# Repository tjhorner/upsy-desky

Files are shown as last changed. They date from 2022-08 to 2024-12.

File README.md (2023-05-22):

# Upsy Desky 

This repository contains the source files for the Upsy Desky, a device which lets you connect your standing desk to any home automation system.

You can buy one on Tindie:



## Need Support?

If you need help with your Upsy Desky, please join the Upsy Desky [Discord server](https://discord.gg/ZHfXKQrSxF) where you can ask for help from the community and myself.

## Repository Structure

At the root of the repository you will find these directories:

- `pcb`: KiCad schematic and PCB design files (CC BY-NC-SA 4.0)
- `enclosure`: Fusion 360 design files and STLs for the enclosure (CC BY-NC-SA 4.0)
- `firmware`: ESPHome configuration files for the stock firmware (MIT)

With these you can make your own Upsy Desky from scratch, or you can make changes to the design and firmware to suit your needs. (If you do, I would love to see it!)

## What's new‽

This is the successor to the [WiFi Standing Desk Controller](https://github.com/tjhorner/wifi-desk-controller), packed with improvements and bug fixes — most notably:

- USB-C port for easy flashing (and because USB-C is cool 😎)
- Runtime firmware configuration -- no more manual flashing or compiling ESPHome to change stuff
- Improved enclosure design with a more snug fit and screw-mounted PCB, allowing for easier repairs and troubleshooting
- Replacing the D1 Mini with an ESP32-WROOM module, providing hardware UART for more reliable desk connection
- A catchier name, because "WiFi Standing Desk Controller" was a mouthful

This revision also fixes some annoying issues from the first version, such as the desk sometimes lowering on startup, or simply not powering at all without a hacky workaround.

## In a nutshell...

As with the original version of this product, it can connect your motorized standing desk to your home automation system. It can read your desk's current height, and set it as well. This lets you create automations that integrate with your desk, for example:

- If you're sitting for too long, raise desk to standing height
- When you leave home, raise desk to max height so the cat can't knock things over
- Have an infinite number of presets for everyone in your household
- Send desk height data to InfluxDB to analyze how often you're sitting vs. standing
- [Publish your desk's height on the internet](https://tjhorner.dev/sitting-or-standing/)

Or whatever else you'd like. The possibilities are endless! As long as the possibilities involve a standing desk.

## Compatibility

Any standing desk that uses RJ45 to connect to the keypad is likely compatible, but the control boxes listed [here](https://upsy-desky.tjhorner.dev/docs/reference/compatibility/) are verified to be compatible.

## Documentation

You can find everything you need in the [documentation](https://upsy-desky.tjhorner.dev/docs/getting-started/).

## Licenses

The ESPHome configs are licensed under MIT; everything else (enclosure and PCB design) are CC BY-NC-SA 4.0. The appropriate license files are available in the root of the repo.

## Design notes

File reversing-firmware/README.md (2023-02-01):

# Reverse Engineering Firmware

This is a special firmware designed to aid in the reverse engineering of new desk control box protocols. You can find the complete reverse engineering guide [here](https://upsy-desky.tjhorner.dev/docs/advanced/reverse-engineering/).

You can flash this firmware on your stock Upsy Desky; no additional hardware is required. It uses ESPHome's [UART debugging feature](https://esphome.io/components/uart.html#debugging) to log all communication between the keypad and control box. You can use this data to reverse engineer the protocol based on the RE guide linked above.

## Customization

Aside from the normal UART parameters like baud rate, it may be helpful to adjust the parameters in the UART debugging component to make the data more readable and easier to RE. Particularly useful is the `after` parameter, which allows you to log a string of bytes after some specified number of bytes, timeout, or delimiter. You can see the specific configuration options in the [ESPHome documentation](https://esphome.io/components/uart.html#debugging).

You may also wish to change the GPIO port to match the RX and TX pins on your control box if the defaults don't match yours. See the [GPIO Pinout](https://upsy-desky.tjhorner.dev/docs/reference/gpio/) mapping to see which RJ45 pins correspond to which GPIO pins.

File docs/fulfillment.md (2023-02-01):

# Order Fulfillment Process

I wrote this out in order to help my future self if I ever go on hiatus or something. But it could be useful if you're starting to sell a similar product and are wondering what the process is like.

## Batch Order & Packing Slips

When ready to start fulfilling orders, export the unshipped orders from Tindie and generate packing slips to print using [this tool](https://github.com/tjhorner/tindie-packing-slip-generator).

## Shipping Labels

Upload the order CSV from Tindie to Pirate Ship to generate the shipping labels. If needed, make sure to split the CSV based on shipping speed (first class, priority, etc).

Print the shipping labels for the batch on a 4x6 label printer.

## Provision & QA Boards

Grab the amount of boards needed for the order, and send each of them through the QA process, which is semi-automated.

Flash the test target firmware to each board, and plug it in via RJ45 to a test host board. Plug a USB-C cable into the host board and watch for six flashes of the host's LED. If it flashes 6 times, the test is complete and QA is passed. Place a QA sticker on the back.

## Assemble Enclosure

If the customer opted for one, put the boards in enclosures and screw them in place.

## Flash Firmware

Flash the stock firmware on each of the boards using [this tool](https://shop.horner.tj/things/upsy-desky/setup/stock), via USB-C.

## Pack & Ship

Place shipping label for the order on the box. Fold the shipping label, place in the box. Put the items in bubble wrap, and place in the box. Seal the box, and ship it off. Repeat until done with batch.

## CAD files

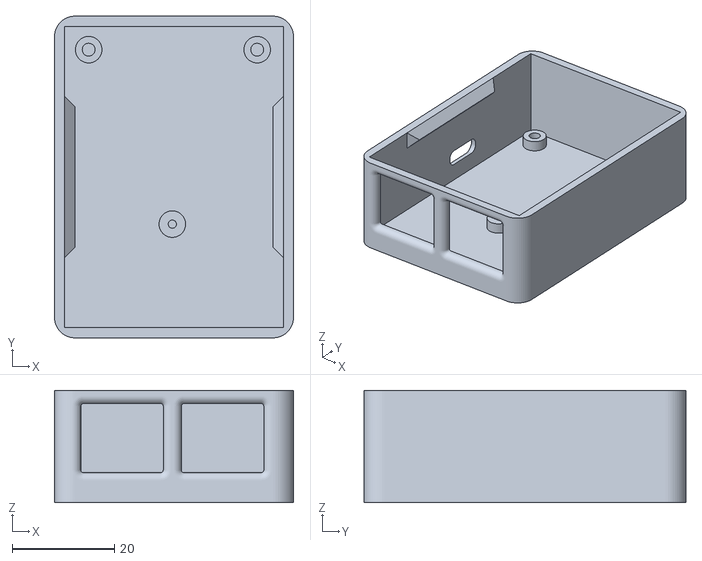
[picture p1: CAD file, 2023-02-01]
enclosure/case.stl
46.8 x 63.0 x 22.0

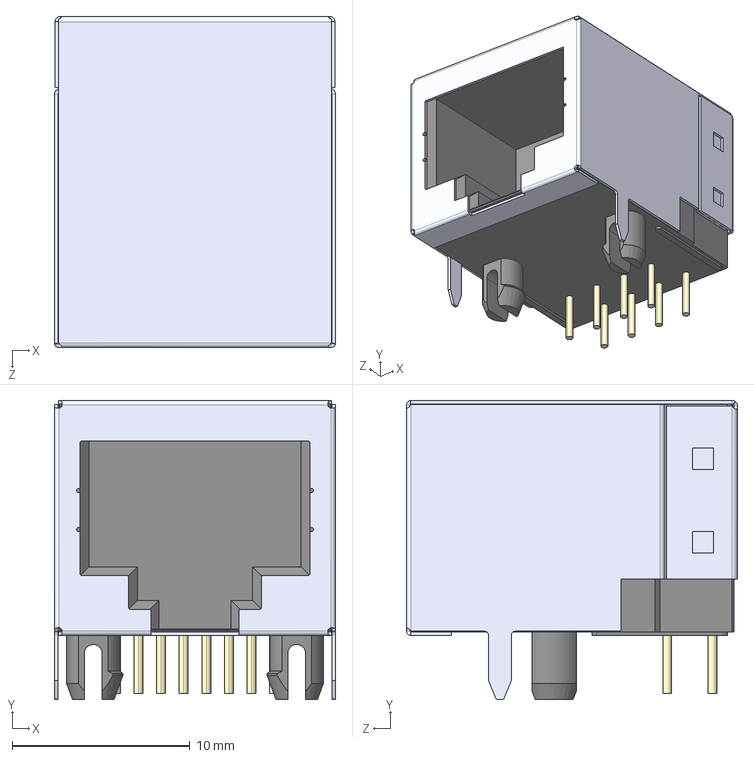
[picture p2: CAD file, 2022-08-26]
pcb/footprints/A-2004-2-4-LPS-N-R.step
15.8 x 16.8 x 18.6 mm

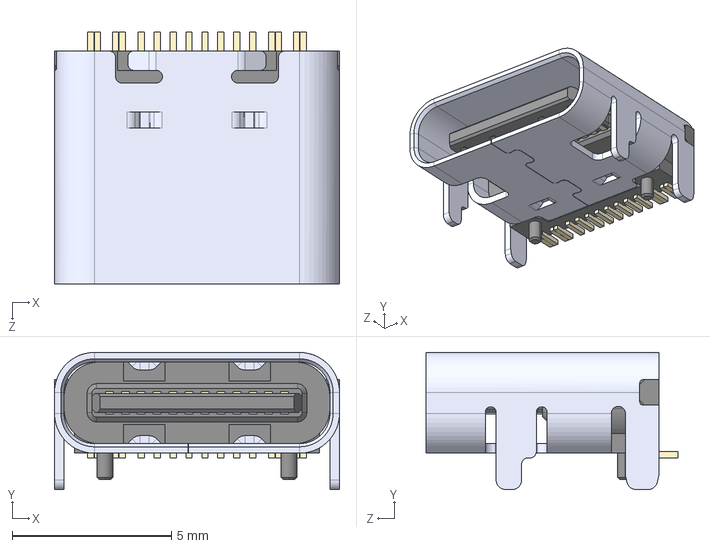
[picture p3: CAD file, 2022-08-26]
pcb/shapes3D/TYPE-C-31-M-12--3DModel-STEP-56544.STEP
8.94 x 4.30 x 7.90 mm

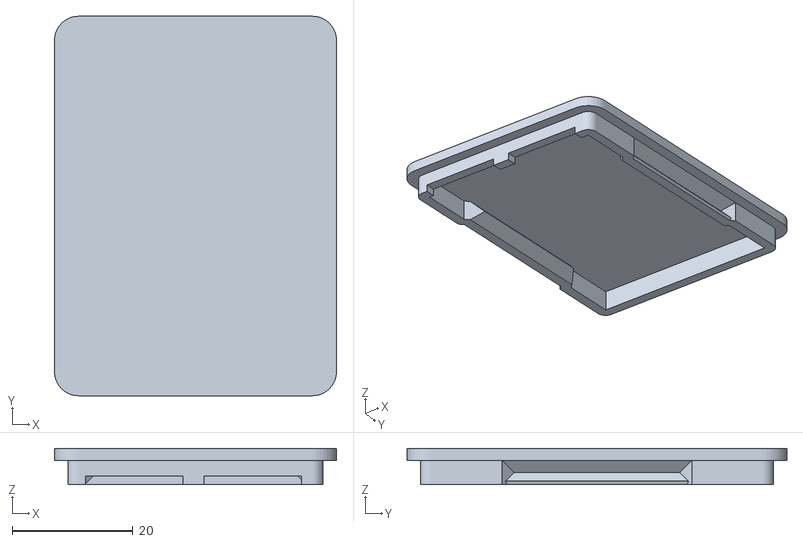
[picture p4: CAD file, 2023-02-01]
enclosure/cover.stl
46.8 x 63.0 x 6.00

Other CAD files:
enclosure/enclosure.f3z

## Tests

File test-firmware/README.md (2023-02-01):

# Test Firmware

This firmware is used to test assembled boards before shipping. In the future I'd like this process to be more automated and comprehensive but this is what I have for now.

## Usage

You will need 2 desk controller boards for this.

1. Flash the `test_host` env to a board. This will be the known-good "host" board that will report the test results.
2. Flash the `test_target` env to the board you want to test. Unplug both from the computer.
3. Connect the host board to the target board with an RJ45 patch cable.
4. Plug the target board into power using micro USB. This will provide power to both boards since the +5V line is shared between them.
5. The LED on the host board should flash a total of 6 times. If it doesn't, this means one of the pins is not connected correctly. Troubleshoot accordingly.

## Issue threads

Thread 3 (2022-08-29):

Support for LINAK controllers

BradleyFord, 2022-08-29:
It would be great if it could support LINAK controllers, these are OEMed to many desk manufacturers and used an RJ45 connection. My IKEA desk is LINAK.

I will most likely buy a device from you when you launch, and can help provide whatever info you need to add support.

(Note their are a few github projects already for the LINAK)

tjhorner, 2022-08-29:
Can you link me to the projects for the LINAK desk? It will give me a good idea of whether support is feasible or not. Thanks!

BradleyFord, 2022-08-29:
The projects I had looked at are:
https://github.com/anetczuk/LinakDeskApp
https://github.com/rhyst/idasen-controller
https://github.com/j5lien/esphome-idasen-desk-controller

AABatteries, 2022-08-29:
+1 on this request, I was just about to ask about LINAK support :) I will be happy to help with hardware testing if need be.

jshep321, 2022-08-30:
Hi guys, I was thinking along the same lines at @tjhorner here!

I measured my (~20yo) LINAK desk (from Kinnarps Sweden).  It was a 29.13V common that simply needs to be connected to wire A for up or wire B for down.  I bought a dirt cheap ESP01 dual relay from aliexpress and connected via ESPHome to HA.

I made a capacitive touch sensor from a different ESP32 (that is part of my office master control) and can control the up/down with that via HA.

My desk has no height sensing so I am currently in the middle of prototyping a ToF distance sensor using HC-SR04 (ultrasonic) and a (3rd!) ESP.  I'm using node red to make Preset heights, but the sensor is currently too noisy to work properly.  I might switch over to a different position sensing method when I reopen this project.  I'm pretty surprised that everything is seamless except the ultrasound.  Delays are imperceptible in this setup.

Do your LINAK desks have position sensors?  My RJ11 is 3 wires only -- V+ (29v) and Up/Down sense.

Happy to share my yaml for the desk motor control if you want.

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

h42y, 2022-08-30:
There is high possibility that system is using hall quadrature encoders to keep the speed and position of the actuators in check. Just sniff them to get position.

tjhorner, 2022-09-06:
So it looks like all the existing projects use Bluetooth to communicate with the control box. I'd say that is the easiest path forward. Since the Upsy Desky has an ESP32 and thus Bluetooth, I recommend using [this ESPHome component](https://github.com/j5lien/esphome-idasen-desk-controller) for now while I look into what it uses for the physical connection.

AlexPotterOnGit, 2022-09-22:
+1 for LINAK. As others ready  to do tests required. I don't think my controller has Bluetooth so I am after wired connection.
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

Tam-Lin, 2022-10-07:
I have an uppy desky now and a linak controller. For this controller, there are 4 wires, and some communication between the desk and controller that happens to communicate the current height.

Tam-Lin, 2022-10-07:
I've done a bit of investigation.  There are 4 wires; from left to right:
1 2 3 x x x x 8

It looks like the wire color could be different, based on the picture above.  In my case, it's
R B Y x x x x Bl

Measurements, which didn't  trigger the desk to do anything:

1 - 2:  -6.6 V
1 - 3: - 4.4 V
1 - 8: - 7.34 V

2 - 3: 0 V
2 - 8: 0 V

3 - 8: 0 V

If I do attach the upsy desky to the desk, it descends to the bottom.

I have a Linak DPG1C controller; I'm not sure about the motor control box.

pi2madhatter, 2023-02-22:
I would throw down the money here and now for LINAK support. I have one that looks identical to the others posted on this, but with slightly different specs. I've attached an image of my label if it helps at all.

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

Ordspilleren, 2023-08-28:
Hi all!
I have been working on exactly this, and I am happy to report that I have a working solution which you can find [in this repo](https://github.com/Ordspilleren/esp32-linak-desk-control). I didn't do this all by myself, so I have given credit where its due.

Integrating it directly within Upsy Desky is unlikely in its current form, simply because I believe esp-idf is a requirement to get the control we need over UART.

It's by no means done yet, but it works reliably for me.

Ordspilleren, 2023-08-28:
> @Ordspilleren You can actually compile your firmware directly for the Upsy Desky if you want; it's just an ESP32 module.

Good point, that's certainly an option if someone wants to go that route. They would still need the custom circuit described in my repo however, unless Upsy Desky can support doing single wire RX and TX and bring the 12V down to 3.3V. I haven't looked at the options in-depth to be honest.

> Why do you think ESP-IDF is required? ESPHome [does support ESP-IDF](https://esphome.io/components/esp32.html#esp32-espidf-framework) but currently it's using the Arduino framework, which is default.

My solution relies on detecting a UART break signal and then clearing the UART FIFO buffer to get the first data byte in the data frame from the table. I also set a couple of ESP-IDF specific options to get the break detection working reliably. Not sure if that is possible with Arduino directly.

With that said, you _can_ call IDF functions from within Arduino, so I guess it should be possible if someone was willing to put in the time.

davidski, 2023-09-28:
It looks like HA is getting 1st party integration with IKEA IDASEN in the 2023.10, which should (not yet tested) include Linak devices. I'm excited to see this land! https://rc.home-assistant.io/integrations/idasen_desk

Ordspilleren, 2023-09-28:
> It looks like HA is getting 1st party integration with IKEA IDASEN in the 2023.10, which should (not yet tested) include Linak devices. I'm excited to see this land! https://rc.home-assistant.io/integrations/idasen_desk

Please note that this integration works via the Bluetooth functionality present in some Linak controllers. This has been possible for several years via [esphome-idasen-desk-controller](https://github.com/j5lien/esphome-idasen-desk-controller) and [LinakDeskEsp32Controller](https://github.com/krzmaz/LinakDeskEsp32Controller).

giantorth, 2024-02-27:
Has anybody gotten Linak support working with an upsy yet?  I suppose I should have checked the issues before I bought one of these ;)

giantorth, 2024-02-27:
I'm not sure this is helpful, but the Linak desks did have a USB adapter for PC control, the USB2LIN06 cable.
You can see pictures of it here: https://github.com/UrbanskiDawid/usb2lin06-HID-in-linux-for-LINAK-Desk-Control-Cable/tree/master/PHOTOS/usb2lin06-HID

I'm curious if it would be possible to use this cable as some sort of bridge for the hardware compatibility issues with the upsy and a linak controller, perhaps with a bit of soldering if necessary.

giantorth, 2025-03-05:
Not sure who's still got these Linak desks, let alone the USB adapter for one, but for those wanting to smarten up these ancient Linak controllers I've written an MQTT service to control my desk using a pi zero and a USB2LIN06 adapter: https://github.com/giantorth/linak-mqtt-ctrl

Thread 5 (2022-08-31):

Adapter Cable Research

tjhorner, 2022-08-31:
There are many different standing desk brands out there, and most of them use the RJ45 pinout that this project does. However, there are a few that do not! How do we add support for them? I think the best solution is to create adapter cables which can easily and cheaply modify the pinout or physical connector so that the Upsy Desky can communicate with the desk.

For example

- LoctekMotion desks
  - Uses RJ45
  - Different pinout (see [here](https://github.com/tjhorner/wifi-desk-controller/discussions/2#discussion-4151398))
  - Solved with a custom cable which is wired differently at one of the terminating ends
- Autonomous.ai desks
  - Uses RJ50
  - Different pinout
  - Solved with a custom cable which terminates in RJ45 at one end and RJ50 at the other

I think this is a good way to solve the problem, but I'm not entirely sure how to manufacture these at scale. I'll be researching different ways to do this.

tjhorner, 2022-09-02:
## Autonomous Desk Adapter
- **Connector**: RJ50 (10p10c)
- **Pins in use**: 5

### Pin Functions

| Position | Color  | Function |
|----------|--------|----------|
| 1        | N/A    | N/A      |
| 2        | N/A    | N/A      |
| 3        | N/A    | N/A      |
| 4        | Red    | Sleep    |
| 5        | N/A    | N/A      |
| 6        | N/A    | N/A      |
| 7        | Orange | GND      |
| 8        | Yellow | RX       |
| 9        | Green  | TX       |
| 10       | Blue   | +5V       |

### Pin Mapping

| Function | RJ45 Position | RJ50 Position |
|----------|---------------|---------------|
| Sleep    | 1             | 4             |
| RX       | 2             | 8             |
| GND      | 3             | 7             |
| TX       | 4             | 9             |
| +5V      | 5             | 10            |
| N/A      | 6             | N/A           |
| N/A      | 7             | N/A           |
| N/A      | 8             | N/A           |

tjhorner, 2022-09-02:
Reached out to a cable manufacturer to get prototypes of the Autonomous adapter cables made based on the above info.

rosstadude, 2022-09-13:
I would be interested and willing to test on my Autonomous desk. Please let me know how much for the cable. Thank you

Jolanrensen, 2022-10-01:
Also willing to test on my locktech desk! I don't have an upsy desky yet, but I'm on the waiting list

Jolanrensen, 2022-11-03:
I now do have one :) Also, I have some ethernet (RJ45) plugs and a crimping tool, so I can modify and test a cable to see if it works on HS01B-1 Locktech desks. Did follow [this](https://github.com/tjhorner/wifi-desk-controller/discussions/2#discussion-4151398) but it seems to have gone silent.
I'm also curious if one or two cables would need to be modified. Since the upsy desky is a passthrough I think the cable to the controller/screen of the desk would also need to be modified as well as a cable to the desk motor itself. Is that right?

tjhorner, 2022-11-03:
Yes, getting the original keypad to work will be tricky and might require some kind of other adapter. For now I am focusing on getting the Upsy Desky working with the control box

Jolanrensen, 2022-11-04:
Alright :) If ever needed, I did find some extra info about passthrough for the keypad: https://github.com/iMicknl/LoctekMotion_IoT/tree/main/packages/esphome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

Jolanrensen, 2022-11-05:
Alright, so I created an adapter cable based on the sources available to me:

RJ45 OG | cat5 OG colors (upsy desky side) | RJ45 Target | Cat5 Target colors (desk side) | HS01B-1 purpose (after rewire)
-- | -- | -- | -- | --
1 | orange/white | 1 | orange/white | RES (needs passthrough for keypad)
2 | orange | 6 | green | RX (needs bridging for keypad)
3 | green/white | 7 | brown/white | GND (needs bridging for keypad)
4 | blue | 8 | brown | TX (keypad should have different GPIO)
5 | blue/white | 2 | orange | 5V (needs bridging for keypad)
6 | green | 4 | blue | SWIM (needs passthrough for keypad)
7 | brown/white | 3 | green/white | (unknown) (needs passthrough for keypad)
8 | brown | 5 | blue/white | PIN 20 (keypad should have different GPIO)

Some clarification: "Passthrough" can mean either ouside the upsy-desky or through it without touching the signal. I don't know if it's needed for the desk to operate but it's what mentioned here https://github.com/iMicknl/LoctekMotion_IoT/tree/main/packages/esphome#hs01b-1
"Bridging" means the upsy desky needs the connection but it also needs to be passed through to the keypad.
Not sure what needs to be done with TX and PIN 20 since they are wired to different GPIOs altogether, both from/to the keypad as from/to the desk controller.

But let's start with just the desk controller as I created the cable for it. Connecting the upsy desky gives it power (since it now has 5v at pin 5), but where do I go from here? I have programming experience for sure, but haven't worked with esphome before, so if I could be pointed in the right direction, that would be great :)

tjhorner, 2022-11-05:
@Jolanrensen excellent research! To test out the firmware you can follow ESPHome's [setup guide](https://esphome.io/guides/getting_started_command_line.html) then try installing the various configs from the repo you linked above ([here](https://github.com/iMicknl/LoctekMotion_IoT/tree/main/packages/esphome)).

Jolanrensen, 2022-11-06:
So the plan is to get that to work as best as possible and then adapt your template to it? :) Cause that sounds doable. I'll report back when I have something working!

Jolanrensen, 2022-11-07:
Small update: I'm able to control the desk from home assistant! (using https://github.com/Jolanrensen/LoctekMotion_IoT) It does seem to stutter a lot XD Not yet sure if that's because of my wiring or the software.

Jolanrensen, 2022-11-08:
Just as a redundancy test, connecting a similar adapter from they keypad to the upsy desky does light up the keypad and displays the correct height, but the desk is uncontrollable, both from HASS, as well as the buttons. Thought so :)
However, to be able to connect both the desk and the keypad to the upsy desky I probably have to make another adapter cable, disconnecting a couple of lanes to free up GPIO ports

Jolanrensen, 2022-11-15:
@ajfriesen That's exactly what I ordered :)
But I would still need a sort of special cable-adapter since some cables need to bypass the upsy desky going straight from the keypad to the desk and some need to go through.

Something like (forgive my drawing):
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
Where
UD: upsy desky
K: Keypad
b: Desk

But hopefully I can soon do some more testing :)

tjhorner, 2022-11-16:
> Just an idea: For mass production it may be easier to look into an adapter board where you punch down cables by yourself?

That's a great idea! Never thought of that. I'll see how the cost compares to custom cables.

Jolanrensen, 2022-11-17:
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

Well, I've got something working :D Using my branch of LocTekMotion https://github.com/Jolanrensen/LoctekMotion_IoT/tree/main I can now control the desk both from the keypad and home assistant :)
There are still some problems:
  - The screen just stays on, not sure why.
  - When the UD just booted, the desk height is NaN until changed, but sometimes the UART gets flooded with 0x00 freezing up and crashing the UD
   - The number buttons and M/A do nothing with the desk. They do get picked up by the software and, in theory, they send their command to the desk, but nothing happens.

However, these problems are most probably software problems :)
My wiring (hopefully including all coloring standards, haha):

cat5 B | cat5 B | HS01B-1 | Upsy Desky side (from desk) | Upsy Desky side (from keypad)
-- | -- | -- | -- | --
1 | orange-white | brown |   |  
2 | orange | white | 5/blue-white/green (RX GPIO17) | 5/blue-white/green (RX bridged from desk GPIO17)
3 | green-white | purple | 7/brown-white/blue (GND) | 7/brown-white/blue (GND)
4 | blue | red | 6/green/black (TX GPIO16) |  
5 | blue-white | green | 8/brown/yellow (5V (VVD)) | 8/brown/yellow (5V (VVD))
6 | green | black |   | 6/green/black (TX or RX from UD pov GPIO19)
7 | brown-white | blue |   | 4/blue/red (pin 20 GPIO21)
8 | brown | yellow | 4/blue/red (pin 20 GPIO22) |  

Connected straight from desk to keypad:
  - 1 / orange-white / brown
  - 2 / orange / white
  - 3 / green-white / purple

Yes, I changed my wiring method a bit to make it easier to work with for my breadboard.

Jolanrensen, 2022-11-19:
My beautiful adapter! It's completely based on the table above.
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

Simply plug the two male plugs in the Upsy Desky and connect the female plug to the keypad and the male plug in the desk controller:
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

It's easy to replicate if you have a small ethernet extension cable (male to female, adhering to cat5 B) where you strip out the middle bit, cut all wires except 1,2, and 3 and then attach two male ethernet plugs using the table above.
If you don't have an ethernet crimping tool, there are also toolless options available:
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

Not sure if it would be possible to manufacture something like this, but doing it yourself can be done in less than an hour :)

rosstadude, 2022-11-19:
This is great!

Jolanrensen, 2023-01-19:
@MrTechGadget 108ms is very specific timing indeed haha. Very cool! I will definitely try that too. I'm currently using a delay of 0ms which is smooth but sometimes "hesitates" a bit. I do think that these timings are very specific to your own setup on the cables, connectors, the motor etc.

backslashV, 2024-01-02:
Hi there, I have a similar desk with an RJ50 keypad connector. I'd like to use an Upsy Desky to make the desk smart, but that device uses an RJ45 connector. Can anyone suggest a way to identify what each of these 5 pins do so I can make a custom RJ50 to RJ45 adapter?
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

tim-vk, 2024-07-24:
Silly question: but what is the pinout that the upsy desky expects?
In the documentation it mentions pin 3 = GND and pin 5 = 5v. But which ones are the RX & TX pins? I couldn't find that in the docs (and i'll probably need to open the pcb files: which i can't).

JesperKuipers, 2024-09-29:
> Silly question: but what is the pinout that the upsy desky expects? In the documentation it mentions pin 3 = GND and pin 5 = 5v. But which ones are the RX & TX pins? I couldn't find that in the docs (and i'll probably need to open the pcb files: which i can't).

https://github.com/tjhorner/upsy-desky/blob/master/firmware/base.yaml
line 19 and line 35

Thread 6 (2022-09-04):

Unable to operate Autonomous desk

ChrisCrewdson, 2022-09-04:
Perhaps it uses a different protocol?
I cut the controller cable with the RJ50 and spliced in an RJ45 on both cut ends, following the pinouts from https://github.com/tjhorner/upsy-desky/issues/5#issuecomment-1235040100
It seems like it should be fine since power and ground at least seem right with multimeter testing.
It does still work with the controller when using two keystone jacks punched down back to back.

When I attach the upsy-desky to the desk, it powers on and I can see it in home assistant, but it does not control the desk or read height.

When plugging in the controller to the upsy-desky, the controller display shows full digits and the backlight powers on
However, the buttons only make the backlight turn on while pressed (the normal behavior), but do not operate the desk and the height is not shown.

The controller is https://www.timotion.com/en/products/controls/tdh6-series and the box is https://www.timotion.com/en/products/control-boxes/tc15-series

tjhorner, 2022-09-04:
The protocol is indeed different. Someone else has reverse engineered the protocol the Autonomous desks use and posted their work in this repo: https://github.com/Stefichen5/AutonomousControl

I do plan on adding official support for Autonomous desks very soon! Need to make the adapter cables then work on adding support in the firmware.

ChrisCrewdson, 2022-09-04:
Thank you! I had just found this discussion which lead me to the same place: https://github.com/tjhorner/wifi-desk-controller/discussions/16

Gast0n87, 2022-09-22:
> Thank you! I had just found this discussion which lead me to the same place: [tjhorner/wifi-desk-controller#16](https://github.com/tjhorner/wifi-desk-controller/discussions/16)

Did you manage to get it working?

ChrisCrewdson, 2022-09-22:
I have not managed to get this working. My first step was to attempt to log the periodic messages from the desk to the controller, but nothing has come through. There might even be a hardware problem since I think the two RJ45 ports on the upsy-desky are tied together and they may need to be separate UARTs: https://github.com/tjhorner/wifi-desk-controller/discussions/16#discussioncomment-3090583
That being said, I haven't managed to get anything working even with just one of the desk or the controller attached at a time.

normanr, 2022-12-31:
fwiw EasyErgo also uses the TiMotion devices.
I have a TC15S control box with a TDH18P controller. Pins are 2,4,7,8,9,10 (black,red,orange,yellow,green,blue) which matches the opening comment (extra black wire on pin 2 though). I haven't been able to verify signals yet, but I'm hoping that a USB to serial cable can be made to work.

normanr, 2022-12-31:
I noticed that the TDH18P has a RJ50 jack in the back of the unit (for a bluetooth dongle, model TWD1), so I checked with a multi-meter and confirmed that pins of the jack seem to be directly connected to the plug. Referring to the functions documented at https://github.com/tjhorner/upsy-desky/issues/5#issuecomment-1235040100 I also confirmed that GND (Orange) and +5V (Blue) are directly connected to the USB plug GND and VCC pins.

I checked the pin voltages at the jack on the TDH18P while it's plugged into the control box and (unsurprisingly) they match the documented functions. RX and TX are near +4.8V and change slightly when the display updates (RX), or when buttons are pushed (TX), they seem to return to +5V when the display is off. Sleep (Red) is +5V when the display is off, and 0.2V when the display is active. Pin 2 (Black) is +5V, but I have no idea what it's used for.

If I plug an cat5 cable directly into the TC15S control box (i.e. with the TDH18P controller disconnected), then pins 3, 5, and 6 also have 5V (and TX and RX are +5V, so no data is being sent or received when the control unit is not attached). Based on the PDFs linked to from https://www.reddit.com/r/esp8266/comments/vlu0om/beginner_standing_desk_project/ I tried shorting pin 7 (GND) to pins 5 and 6 and confirmed that they cause the desk to move up and down. I didn't try the same with pin 3 (and didn't have access to pin 1, because the cat5 cable only connects to pin 2 through pin 9).

normanr, 2022-12-31:
I found some internal photos of the bluetooth dongle in the [fcc filing](https://fcc.report/FCC-ID/W6JTWD1) which show that only pins 4, 8, 9, and 10 are used, so that's nice confirmation too.

Andrerm124, 2023-01-02:
Very interested in this topic, I'm not experienced in this field so can't really contribute, but @normanr if you find anything it'd be really interesting if you could share 🙂

JohnAZoidberg, 2023-01-09:
I've got a table with TDH20P handset and TC15S Control Box.
The UART pins match https://github.com/tjhorner/upsy-desky/issues/5#issuecomment-1235040100
And the protocol matches https://github.com/adfinis/muuvctl#serial-protocol

JohnAZoidberg, 2023-01-10:
To clarify what I did:
I got RJ50 (10P10C) and RJ45 (8P8C) connectors and crimped them together on a cable.
Then using an RJ45 breakout board I connected the TX,RX and GND pins to a cheap logic analyzer.
I plugged RJ50 into the back of the handset.

After confirming the protocol looks fine, I connected it to a UART to USB adapter.
This would cause issues when I connected something to TX on the adapter, so I first connected the cables's TX to the adapter's RX and then the cable's RX. With pyserial i could snoop the traffic.

muuvctl doesn't seem to work solidly when connecting RJ50 to the control box. It can get the height sometimes but usually it displays the wrong byte.

testventure, 2023-02-14:
Dang should have checked here before I bought it.  But I will eagerly await an update to handle the TiMotion desk.

StillAlyve, 2023-04-22:
I've also got a TC15s controll box with pins, that match [these](https://github.com/tjhorner/upsy-desky/issues/5#issuecomment-1235040100)  on the handset.

Would I be able to run the python code on a pi using a console cable?

ericfri, 2023-08-11:
Any updates on adding Autonomous desk support?

tjhorner, 2023-08-11:
Unfortunately I haven't had the bandwidth to investigate this further as I've been very busy at my dayjob, and I don't have any Autonomous desk hardware to properly test it. However, Autonomous desk support is still something I would like to add in the future. I appreciate the efforts of everyone who has contributed in this thread — all the info presented here looks very useful for when I am able to pick this back up.

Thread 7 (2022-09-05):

Geekdesk Compatibility

J-Camping, 2022-09-05:
Hello! I recently received the Upsy desky and would like to try it out on my geekdesk.
It looks like pin 3 has 5v and pins 1,5,7,8 all appear to be grounds.

The controller is labelled ey-h6032c, and does also have an rj11 port. I found this manufacturer page, but it didn't seem to have much information. https://www.eyoungonline.com/products/pro_51.html

Guessing at a minimum I would need to make a custom cat 5 cable to swap the 5v and gnd to match the upsy desky?

Want check with you before breaking anything too badly.

Thanks,

James

tjhorner, 2022-09-05:
Hi! Yes, at minimum you would need to make the +5V and GND match the pinout on the Upsy Desky. The pinout is available [here](https://github.com/tjhorner/upsy-desky/wiki/GPIO-Pinout).

After that I would go ahead and try out the stock firmware and see if any of the existing protocol decoders work. If not, then more reverse engineering work is probably required.

J-Camping, 2022-09-07:
I reversed the wires for 5v and gnd, the board powers up and I can connect to the web interface. As soon as it turns on, the board goes to its highest or lowest level. I haven't moved any other wires yet.

When either uplift or jarvis is selected and I select preset 1 it goes to the bottom, preset 2 doesn't do anything, preset 3 goes to bottom, preset goes to 4,  and the slider doesn't do anything.

Let me know what I can do to help with any reverse engineering, and thank you for creating this and the help!

Handset photos attached.
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

cturra, 2023-02-16:
is there anything i can do to help out? happy to pull things apart on mine also.  i’m really interested in having my geekdesk supported

thomascantrellsea, 2023-10-27:
I wanted to record a few things I worked out:
- Do not plug your Upsy Desky into the Geekdesk MAX (EY-H6032C) without an adapter cable. I fried the Upsy Desky pretty quickly doing this. Desk is doing fine. It's my bad, I'll order another. This is very likely because of the differences in the 5V/GND pins.
- If pin 3 and pin 5 are flipped, it seems likely that one can use Upsy Desky though looking at the pinout.

Pinout from my EY-H6032C control panel cable matched up with your image (JCH35-TLD-V3)

1. White - PTC1
2. Yellow - PTC2
3. Red - VCC = +5V
4. Green - PTB5
5. Black - GND
6. Blue - PTB6
7. Manual up - not connected on cable - see [1]
8. Manual down - not connected on cable - see [1]

Notes:

1. Jumping 3 to 7 or 8 causes the desk to go up and down. This matches with https://github.com/Hypnopompia/photon-desk/blob/master/README.md
2. Also see https://forums.adafruit.com/viewtopic.php?p=649290, though the underlining control panel processor seems slightly different (JCH35-TLD-V2)
3. Appears that Jiecang has slightly different wirings between the Geek Desk and other desks.

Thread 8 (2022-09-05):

Support for wn17cm2 controller

AnalogAyub, 2022-09-05:
I was able to set up the UpsyDesky easily, but the unit would not power on with just the RJ45 from the desk controller box. Once connecting a USB-C, the unit was detected by Home Assistant but would not control the desk or detect a height. Additionally, the desk keypad daisy-chained through the UpsyDesky would not control the desk.

Here's what the box looks like:
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

tjhorner, 2022-09-06:
Interesting, could you verify that the +5V and GND lines are on the correct positions? You can find the RJ45 pinout [here](https://github.com/tjhorner/upsy-desky/wiki/GPIO-Pinout). If they aren't in the correct place, you may need a special cable.

seanford, 2022-09-06:
Same for the WN17CM3, which I assume will have the same pinout.  This is the controller for the Monoprice desks.

seanford, 2022-09-06:
https://www.kontive.com/products/lifting_table_part/17.html

Maybe they can help.

AnalogAyub, 2022-09-07:
> Interesting, could you verify that the +5V and GND lines are on the correct positions? You can find the RJ45 pinout [here](https://github.com/tjhorner/upsy-desky/wiki/GPIO-Pinout). If they aren't in the correct place, you may need a special cable.

Honestly, I'm out of my depth here 😬

Providing power through USB-C was no problem, though.

seanford, 2022-09-26:
If anyone figures out the pin out for the controller, I can make a cable and test it out.

seanford, 2022-10-15:
Any instructions on how to test the pinouts so I can help move this along?

tjhorner, 2022-10-16:
@seanford I recommend getting an RJ45 breakout board [like this one](https://www.amazon.com/Treedix-Connector-Breakout-Compatible-Unassambled/dp/B08HGS5G8N) so you have somewhere to attach multimeter leads. Then follow this guide: https://github.com/tjhorner/wifi-desk-controller/wiki/Desk-Compatibility

Basically, just use a multimeter to find the position of the +5V and GND pins. After that we can start figuring out which pins transfer which data, if it uses serial, etc.

Jaharmi, 2022-11-18:
I have a desk with a WN17CM3 controller. The control pad is wired with an RJ45. I have found the following pinouts and color coding.

**Control panel wires**

|  **Wire color** | **Pin label** |
|  ----- | --- |
| Red | Vin |
| Blue | Rx |
| Yellow | Tx |
| Black | Gnd |

**RJ45 pinout**

| **RJ45 pin** | **Wire color** | **Note** |
|  ----- | ----- | ----- |
| 1 | Orange | |
| 2 | Blue | Rx from control panel |
| 3 | Black | Gnd from control panel |
| 4 | Yellow | Tx from control panel |
| 5 | Red | Vin from control panel |
| 6 | Orange | |
| 7 | Orange | |
| 8 | Orange | |

Below are pictures of my evidence:

1. the disassembled control pad, where the circuit board labels the wires
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

2. the RJ45 cable coming from the control pad (bottom and top, since it was difficult to see the colors on all the wires from the bottom)
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

Jaharmi, 2023-01-31:
With my just-arrived Upsy Desky, I see the same thing as @AnalogAyub.

1. I was able to set up the UpsyDesky easily.
2. Connected USB-C, the unit was adopted by ESPHome and detected by Home Assistant.
3. The unit would not control the desk or detect a height. I tried both decoders.
4. The desk keypad daisy-chained through the Upsy Desky would not control the desk.
5. The unit stopped responding with just the RJ45 from the desk controller box. I tried connecting to the Upsy Desky Web interface and it timed out.

I will double-check for the +5V and GND pins from the controller box.

Once I've found that, will the device need a debug firmware installed? Or is there something I can change in the (very minimal) ESPHome config?

Jaharmi, 2023-01-31:
I think RJ45 pin 2 is +5v and 3 is GND. I've also posted in the reverse engineering discussions area.

swoga, 2023-08-28:
i reverse enginieered the pinout and protocol some time ago, maybe this will help you: https://github.com/swoga/standingdesk

Jaharmi, 2024-02-02:
@swoga Awesome. I’ve been wondering about this for years! Do you have any thoughts on how this could integrate into Upsy-Desky / ESPHome?

swoga, 2024-02-02:
@Jaharmi
My plan is to write a custom component for ESPHome, but I haven't gotten around to it yet. It's definitely still on my to-do list.

Jaharmi, 2024-02-02:
@swoga If this fit in with Upsy-Desky, I’d be a fan. :) That would give it things like the Upsy-Desky local Web interface. I already have an Upsy-Desky and just never figured out how to get from beyond the pinouts to do anything else.

Looking at the [related component](https://github.com/tjhorner/esphome-standing-desk), the C++ part is currently beyond me.

Jaharmi, 2024-02-03:
@swoga Does this state diagram seem to handle what you found in the serial protocol for the WN17CM3? I am trying to understand the protocol and maybe do something with it. This is probably my first state diagram ever so I may have mixed it with a flow chart.

```mermaid
stateDiagram
    [*] --> CMDBEGIN
    CMDBEGIN --> CMD
    CMD --> DISPLAY: D
    CMD --> KEY: K
    CMD --> REQUEST: R
    CMD --> ACKNOWLEDGE: A
    DISPLAY --> HEIGHT
    HEIGHT --> HEIGHTCKSUM
    HEIGHTCKSUM --> CMDEND
    HEIGHT --> COMMAOPT
    COMMAOPT --> HEIGHTCKSUM
    KEY --> DONTCARE
    REQUEST --> DONTCARE
    ACKNOWLEDGE --> DONTCARE
    DONTCARE --> CMDEND
    CMDEND --> CHKSUM
```

Jaharmi, 2024-02-03:
@swoga Does this state diagram seem to handle what you found in the serial protocol for the WN17CM3? I am trying to understand the protocol and maybe do something with it. This is probably my first state diagram ever so I may have mixed it with a flow chart.

```mermaid
stateDiagram
    [*] --> CMDBEGIN
    CMDBEGIN --> CMD: colon
    CMD --> DISPLAY: D
    CMD --> KEY: K
    CMD --> REQUEST: R
    CMD --> ACKNOWLEDGE: A
    DISPLAY --> HEIGHT
    HEIGHT --> HEIGHTCKSUM: decimal number as string
    HEIGHTCKSUM --> CMDEND: semicolon
    HEIGHT --> COMMAOPT: comma
    COMMAOPT --> HEIGHTCKSUM
    KEY --> DONTCARE
    REQUEST --> DONTCARE
    ACKNOWLEDGE --> DONTCARE
    DONTCARE --> CMDEND: semicolon
    CMDEND --> CHKSUM
```

seanford, 2024-02-05:
> Vin from control panel

@tjhorner it seems that the pinouts for this controller are the same as other controllers, but the protocol is different.  With the information provided by @swoga, is it possible to write a new decoder for this controller?   I'd do it myself if I thought I could...lol

KiloHotl, 2024-02-06:
Hi, I recently purchased the WN20CM2NR V1.33 (printed on the PCB). The RJ45 on the control panel only has 4 wires:

<p dir="auto" style="box-sizing: border-box; margin-top: 0px; margin-bottom: 16px;"><strong style="box-sizing: border-box; font-weight: var(--base-text-weight-semibold, 600);">RJ45 pinout</strong></p>

RJ45 pin | Wire color | Note
-- | -- | --
1 |  |  
2 | Black | Rx from control panel
3 | Green | Gnd from control panel
4 | White | Tx from control panel
5 | Red     | Vin from control panel
6 |  |  
7 |  |  
8 |  |

Using a D1 mini and some research, I was able to intercept the UART comms but using the @swoga baud rate (19200), the data is different. This is the log:

```
[uart_debug:114]: <<< 3A:57:4E:31:38:48:33:32:2E:56:32:2E:30:30:2E:31:39:31:38:2E:30:30:31:42:46:3B
[uart_debug:114]: >>> 3A:4C:4C:39:38:3B
[uart_debug:114]: <<< 3A:57:4E:31:38:48:33:32:2E:56:32:2E:30:30:2E:31:39:31:38:2E:30:30:31:42:46:3B:3A:41:34:31:3B
[uart_debug:114]: <<< 3A:41:34:31:3B
[uart_debug:114]: >>> 3A:44:31:30:39:44:45:3B
[uart_debug:114]: >>> 3A:41:34:31:3B:3A:44:31:31:35:44:42:3B
[uart_debug:114]: <<< 3A:4B:20:33:4D:45:42:3B:3A:41:34:31:3B
[uart_debug:114]: >>> 3A:41:34:31:3B
[uart_debug:114]: <<< 3A:4B:20:33:42:45:30:3B
[uart_debug:114]: >>> 3A:44:31:31:35:44:42:3B
[uart_debug:114]: <<< 3A:41:34:31:3B
[uart_debug:114]: >>> 3A:41:34:31:3B:3A:44:31:30:39:44:45:3B
[uart_debug:114]: <<< 3A:4B:20:32:4D:45:41:3B:3A:41:34:31:3B
[uart_debug:114]: >>> 3A:41:34:31:3B
[uart_debug:114]: <<< 3A:4B:20:32:42:44:46:3B
[uart_debug:114]: >>> 3A:44:31:30:39:44:45:3B
[uart_debug:114]: <<< 3A:41:34:31:3B
```
I´m tryong to analyze the data in order to identify what`s going on

KiloHotl, 2024-04-05:
hi @swoga could yo develop the custom component? I been trying for several weeks and nothing worked.

iambucketdotcom, 2024-08-23:
Hi! I, too have this controller and have only been able ot get the UART messages to work with upsy desky. am I understanding correctly that more is still needed to make this unit work?

Thanks - Bucket

seanford, 2024-08-23:
Unfortunately, I don't think it is going to happen.

seanford, 2024-11-29:
Is it safe to say that this control box will no be supported by Upsy Desky?  Just wanted to know if I should continue to monitor this project for an update or just move on.

Jaharmi, 2024-12-15:
Unless someone like @swoga can figure out a component that handles the communication, I don’t see it happening. Although I’m very interested in making it work, it’s beyond my current understanding.

I’m still not sure why the Upsy-Desky doesn’t seem to get power from the WN17CM3 controller. It seems like _that_, at least, should be working, given the pinouts we’ve all found.

I am not sure whether or not my Upsy-Desky’s RJ45 ports even work.

I also don’t know if there’s a way to capture and decode the serial/UART communication. Maybe something could be done with the UART Bus component in ESPHome. 🤷

Jaharmi, 2025-01-04:
**Update:** I set up the reverse engineering firmware with the UART settings from @swoga. Since I could not set a `stop_bit` of `0`, I set it to `1`.

With this firmware, I was able to capture sequences that appear to correspond to the investigation by @swoga. I can confirm that the display on the connected keypad — which initially started out at `8.8.8` — did update with the expected desk height values that I normally see when the Upsy-Desky is not in the loop.

I am attaching the following files:
- firmware YAML I used: [upsy-desky-WN17CM3-reverse-engineering-uart-debug.yaml.txt](https://github.com/user-attachments/files/18307881/upsy-desky-WN17CM3-reverse-engineering-uart-debug.yaml.txt)
- log data showing the commands going back and forth successfully: [upsy-desky-WN17CM3-uart-logs-all-buttons.txt](https://github.com/user-attachments/files/18307880/upsy-desky-WN17CM3-uart-logs-all-buttons.txt)

Rough sequence of events from that test:

1. Flashed firmware to Upsy-Desky via USB and let it start up until I could see logs
2. Connected WN17CM3 controller (standard Ethernet cable with 2x RJ45) to Upsy-Desky
3. Connected keypad with its cable (RJ45) to Upsy-Desky
4. Keypad displayed "8.8.8" (I don't think the display changed during the testing)
5. Pressed Up button
6. Pressed Down button
7. Pressed preset button "1" and pressed it again to stop
8. Pressed preset button "2" and pressed it again to stop
9. Pressed preset button "3" and pressed it again to stop
10. Pressed preset button "4" and pressed it again to stop
11. Pressed button "M"
12. Disconnected controller and keypad from Upsy Desky

Jaharmi, 2025-01-04:
I refreshed the Upsy-Desky with similar firmware to what I used above, but changed back to the reverse engineering firmware’s `log_hex` lambda, rather than `log_string`. I didn’t make any other changes.

Here is the log capturing in hex: [upsy-desky-WN17CM3-uart-hex-logs-all-buttons.txt](https://github.com/user-attachments/files/18307921/upsy-desky-WN17CM3-uart-hex-logs-all-buttons.txt)

I followed the same rough sequence, trying to press each button at least twice. The display correctly showed the desk height when I connected the keypad and controller to the Upsy-Desky. It also updated as I raised and lowered the desk with the up/down buttons and presets. It also flashed when pressing the “M” button.

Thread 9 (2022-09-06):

Questions on what I have seen so far...

jhspyhard, 2022-09-06:
I have just a few questions based on playing with the Upsy-Desky over the weekend:

1. Is it to be expected behavior that after setting artificial min / max height values in UD, that the desk's keypad will still allow raising and lowering outside of those limits? Is there any way to get the UD to force the keypad to respect those limits?
2. I'd like to experiment with setting up the webserver and API with HTTPS. Is SSH to the device something that can be turned on? Or maybe it's possible to specify the webserver cert / key values through the YAML config somehow?
3. On that note, is there documentation on all of the available YAML config options which are available through this unit?
4. My Jarvis desk only has up and down controls, but I would love to be able to set some button presets using the UD and be able to recall them using the standard API method. Is there maybe an undocumented API method for setting those button presets on the UD itself if those memory locations don't exist in the desk's controller?

Super cool little device!  Thanks for a neat IOT gadget!

tjhorner, 2022-09-06:
1. Yes. I believe I can make it sync with the keypad — I'll look into it.
2. All of the options for the web server are available [here](https://esphome.io/components/web_server.html), but it doesn't look like it supports TLS. Personally I would use a reverse proxy that adds TLS.
3. The firmware is powered by ESPHome; all of its configuration options are documented [here](https://esphome.io/).
4. Not currently, but I can definitely add that! I'll target it for the next firmware update.

zeel01, 2022-09-25:
I was also wondering about the ability to store the presets (for Uplift). Modifying the stored data on the desk, be it the min/max height, the presets, or possibly the calibration values? All would be really cool. It would also be cool to be able to read those values out.

I was also a little surprised to learn that the min/max values are defined in the firmware rather than being pulled from/stored to the desk controller.

tjhorner, 2022-09-26:
> I was also a little surprised to learn that the min/max values are defined in the firmware rather than being pulled from/stored to the desk controller.

Unfortunately the desk does not report the min/max height to the keypad (and it's pretty finicky to set at runtime with ESPHome) so I'm not sure how feasible this is to change

zeel01, 2022-09-26:
I figured it was something like that.

tjhorner, 2022-10-02:
Closing this issue now. Let me know if you have any more questions @jhspyhard!

Closed 2022-10-02.

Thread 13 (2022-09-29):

Support for LoctekMotion/FlexiSpot desks

Jolanrensen, 2022-09-29:
Looks like most of the work is already done:
https://github.com/iMicknl/LoctekMotion_IoT
I think it would be awesome to have some sort of merge between these projects so that a clean all-in-one (no soldering) solution might also exist for Loctek desks.

tjhorner, 2022-10-01:
Definitely on the roadmap! Will need an adapter cable as noted in #5.

Jolanrensen, 2022-10-01:
Awesome! So same connector, different pinout. That's a bit more tricky than expected, but at least it's the same connector :)

Jolanrensen, 2022-10-13:
I ordered one! Order number #351096
If you already have access to an adapter for that desk for me to try, please let me know! Otherwise I'm also willing to wait for the upsy desky until you can ship it together with an adapter. That's fine by me :) let me know how I can be of help

Jolanrensen, 2022-11-03:
Upsy desky in the house! Now I just need an adapter :) (or a small guide on how to rewire the cables and make an adapter cable)

Jolanrensen, 2022-11-07:
I'll move my software findings here, so the adapter research (https://github.com/tjhorner/upsy-desky/issues/5) can happen in the right issue. Using the adapter described in that issue and my adapted version from LoctekMotion_Iot: https://github.com/Jolanrensen/LoctekMotion_IoT/tree/main

I now have the following working:
- up/down switch (requires virtual screen to be turned on)
- min/max height
- cover up/down/stop
- target height in cm
- 90% of the time smooth motion and no crashes anymore on the upsy desky

I did find that we probably cannot use the upsy desky templates atm, since those assume setting a pin on/off will control the desk, while LoctekMotion (and more) desks require uart streams instead. We could however maybe generalize that to a switch that should be turned on instead since that's how I got it to work. Also, the target height seems to work very accurately :), no +0.4 needed.

Now, getting the screen and buttons to work is next. I'm curious to see what I can do with those. Since the target height works so well from home assistant, I might connect the buttons directly to home assistant as well, allowing them to map to anything you'd like to happen... Don't know yet. The LocktekMotion_Iot project simply captures the signal from the buttons and activates a switch which then sends the signal to the desk again, but the preset buttons don't seem to do anything for me atm, so I'm not sure where those presets are physically saved.

Jolanrensen, 2022-11-08:
@tjhorner btw, is there a reason you use "return id(desk_height)->get_last_read() > x;" instead of "return id(desk_height).state > x;"? Is that for performance or for something else?

tjhorner, 2022-11-08:
@Jolanrensen It's so the automation is more responsive. The state is published less often than the height is read.

Jolanrensen, 2022-11-21:
Additionally fixed in my branch (https://github.com/Jolanrensen/LoctekMotion_IoT/tree/main)
  - Target height in cm now always lands on the right number. Even if it overshoots at first, it will go up/down till it hits the correct height exactly. (Can be quite comical sometimes)
  - Buttons 1, 2, 3 don't work passed through to my desk for some reason. However, you can now set 3 presets cm in Home Assistant (saved in EspHome for when Hass is offline) where the desk will move to

Need to decide what to do with M, A buttons. Maybe I'll recreate some sort of save-function.

Jolanrensen, 2022-11-23:
Pressing M and then 1, 2, or 3 saves the current desk height to the respective preset. Press M again (or any of the other buttons) to cancel.
Unfortunately, the screen doesn't display that you're saving something since the saving functionality of the desk itself doesn't seem to work for me in this setup

r14n, 2023-10-24:
What's the status of Flexispot support?  There's some decent looking ones on Amazon

Jolanrensen, 2023-10-25:
@r14n I've been using my [adapter](https://github.com/tjhorner/upsy-desky/issues/5) and [esphome file](https://github.com/Jolanrensen/LoctekMotion_IoT/blob/main/packages/esphome/hs01b-1_upsy_desky.yaml) successfully for a couple of months now. It's not perfect but it works.

r14n, 2023-10-26:
> @r14n I've been using my [adapter](https://github.com/tjhorner/upsy-desky/issues/5) and [esphome file](https://github.com/Jolanrensen/LoctekMotion_IoT/blob/main/packages/esphome/hs01b-1_upsy_desky.yaml) successfully for a couple of months now. It's not perfect but it works.

Do you think it would work with this one?  Bit hard to tell if the controller is RJ-45.

https://www.amazon.com/gp/product/B0CHVQ5LCL/ref=ox_sc_act_title_1?smid=A3686AOLDPXXOD&th=1

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

Which desk model do you have btw?

Jolanrensen, 2023-10-26:
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

That looks like a completely different controller. Probably RJ-45 since most desks are controlled using that, but we can't be 100% certain. Might also require a different adapter compared to mine. I've got a HS01B-1 controller.

r14n, 2023-10-26:
Are we able to identify this controller?  Searching for your HS01B-1 is not really turning up useful results (as far as desks I can purchase right now)

Keypad：
E2 Pro: 4 Presets Buttons with USB Ports
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

Jolanrensen, 2023-10-26:
> @Jolanrensen also, are you selling your adapter or willing to? Wishing for an "off the shelf" solution, as I'm familiar with homeassistant, but my electrical/wiring skills are very minimal. Seems like the upsy-desky isn't currently totally plug n play with flexispot. I'm also trying to keep my desk budget < $300 including additional "smart" hardware.

Haha I'm flattered, but my electrical skills aren't sell-worthy, plus I can't test it with your desk to see if it would work. Besides, my skills were minimal too before starting. I opted for the upsy-desky over a general ESP board since it already had a case and RJ45 ports. There are many toolless connectors that allow you to more easily make an adapter like mine, but nonetheless it will require some effort on your side. AFAIK there's no off-the-shelf solution for Flexispot desks.

Loic691, 2024-06-11:
Hi To follow this thread.
I just bought an E7 flexispot with this screen
A chance to get it work with Upsy ?
What kind of job we have to produce for flexipot compatibility ?
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

garymc, 2025-03-27:
Would be interested to know if anyone has made this work with Flexispot desks.

Ramiel99, 2025-05-16:
One more vote for Flexispot. I have E7Q (https://flexispot.co.uk/4-leg-standing-desk-e7q)

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

L-e-c-o, 2025-08-09:
Great project, I was wondering if there were any updates on compatibility with Flexispot ?

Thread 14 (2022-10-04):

Jarvis Desk V2 Hardware Target Height requires two commands

Trinnik, 2022-10-04:
I recently received my order for the V2 hardware to hookup to my Fully Jarvis desk (fully assembled). This specific desk uses the uplift decoder. I have the desk working and hooked up to Home Assistant.

When attempting to make the desk go to it's maximum or minimum height, it always requires two commands to be sent. For instance, the max height of my desk is 49.2 inches, however, when I tell the desk to go to 49.2 it will always stop at 43.2. If I send the command again to go to 49.2 it will complete it's travel and reach max height of 49.2. The same thing happens on the way down, my minimum is 30.0 inches, however, it will always stop around 35.2.

A separate issue I noticed, I have to set my limits slightly above and below the reported min and max heights to actually reach them. Otherwise they always stop .3 inches before each value (using the hardware button will get me all the way).

tjhorner, 2022-10-06:
Thanks for the information! I will look into a fix for this.

SnooSnooKachu, 2022-10-06:
I'm experiencing the same thing. I find the further I ask the desk to move in one jump, the further off the end result is. For example, when I ask it to move from 27.7" to 47.2", it stops moving at 41.6". But if I ask it to go from 27.7" to 33.1", it stops at 33.0".

Trinnik, 2022-10-07:
Seems like the timeout in template.yaml needs to be increased from 10 seconds to 20 seconds. Timing my desk it takes 15 seconds to move it's full range, 20 should be enough to cover most cases. Changing this on my device solves this issue.

Also seems like there is a related issue already in that repository. tjhorner/esphome-standing-desk#1

tjhorner, 2022-10-08:
@Trinnik I’m glad that change works for you, I will go ahead and update the timeout to 20 seconds in the stock firmware so others don’t encounter this in the future.

@SnooSnooKachu could you also verify that increasing the timeout fixes the issue?

Thanks all!

SnooSnooKachu, 2022-10-11:
@tjhorner, where can I get this firmware? The latest I see in [this Github](https://github.com/tjhorner/upsy-desky/releases) is v0.1.1. I flashed that onto the device, but it didn't fix anything. I also tried the web flash [here](https://shop.horner.tj/things/upsy-desky/setup/stock), but that just reflashed the v0.1.1 I already had.

tjhorner, 2022-10-11:
@SnooSnooKachu I just released version 0.1.2 that includes a fix for the issue. I had assumed you had your own ESPHome config, my bad! You can flash it from [here](https://shop.horner.tj/things/upsy-desky/setup/stock) now.

SnooSnooKachu, 2022-10-11:
@tjhorner I was able to flash the new firmware and it works like a charm!

tjhorner, 2022-10-11:
Awesome, thanks for confirming. I'll close this issue now :)

Closed 2022-10-11.

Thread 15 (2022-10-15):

IKEA UPPSPEL support

murraythegoz, 2022-10-15:
Hi,

asking for support for the IKEA's UPPSEL
controller seems to be a rebranded JCB36N2
(https://www.jiecang.com/JCB36N2-pd45762211.html)

Works partially.

I set both uplift and jarvis template.
All 4 desk preset works (both from web page and via MQTT)
Current height is not handled.

How can I help debugging?

thank you

m.

murraythegoz, 2022-10-15:
A small update.
desk height is handled, but there is an offset.

Lowest height: 72 cm

height #1: 108 cm
reported height #1: 26 cm

height #2: 72 cm
reported height #2: 25.9 cm

height #3: 120 cm
reported height #3: 26 cm

murraythegoz, 2022-10-15:
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

murraythegoz, 2022-10-15:
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

murraythegoz, 2022-10-15:
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

tjhorner, 2022-10-16:
Thanks for the detailed report! I can make a separate decoder which offsets the height by -72 cm and send that to you for testing. I'll let you know when that is available.

murraythegoz, 2022-10-17:
Thank you,

please let me know if in the meanwhile can help somehow (e.g. how to check whether the problem is due not only to offset or also different way of handling/decoding actual height)

murraythegoz, 2022-11-04:
Hi any update?
May I help somehow?

thanks

tjhorner, 2022-11-05:
Hi @murraythegoz, sorry for the delay. A lot on my plate right now! I should have a firmware for you to test this weekend.

nicholasgk, 2022-12-16:
I had the same issue with my [Omnidesk Pro](https://theomnidesk.com.au/pages/2020). I found that the file [uplift_decoder.cpp](https://github.com/tjhorner/esphome-standing-desk/blob/master/components/standing_desk_height/uplift_decoder.cpp) on line 27, was only looking for a value of 0 or 1. The desk was returning values up to 4. I think it is due to mm vs inches. I changed this one line to
`if (b == 0x00 || b == 0x01 || b == 0x02 || b == 0x03 || b == 0x04) {
`
and it started returning the correct height values.

I am not a C++ programmer, so there probably is a better way to write this. Hope this helps.

murraythegoz, 2022-12-16:
> I had the same issue with my [Omnidesk Pro](https://theomnidesk.com.au/pages/2020). I found that the file [uplift_decoder.cpp](https://github.com/tjhorner/esphome-standing-desk/blob/master/components/standing_desk_height/uplift_decoder.cpp) on line 27, was only looking for a value of 0 or 1. The desk was returning values up to 4. I think it is due to mm vs inches. I changed this one line to `if (b == 0x00 || b == 0x01 || b == 0x02 || b == 0x03 || b == 0x04) { ` and it started returning the correct height values.
>
> I am not a C++ programmer, so there probably is a better way to write this. Hope this helps.

Yup. this made the trick!

I'd instantiate a new variant with the suggested change, to avoid scramble working variants.

Thank you!

pedrams1, 2023-02-05:
Tested this and confirming it resolves the issue reported here - https://github.com/tjhorner/wifi-desk-controller/discussions/18

Thank you so much for this!!! The desk is working perfectly now :)

tjhorner, 2023-02-06:
@pedrams1 could you provide the model number for your desk's control box? I'd like to add it to the list of supported desks in the documentation. Thanks!

Closed 2023-02-01.

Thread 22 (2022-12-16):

ROL ERGO Support

magnussp, 2022-12-16:
I'm trying to check see if I can get Upsy-Desky to work with a ROL ERGO GF-470 (Swedish manufacturer of standup desks, I do believe they have sold some controllers to IKEA as well). This is what I have found so far.

This is a picture of the circuit board of the controller box which the original keypad for the desk connects to.
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

This is how the inside of the keypad looks like
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

What we can conclude from this is that according to the [Desk Compatability](https://github.com/tjhorner/wifi-desk-controller/wiki/Desk-Compatibility) the ROL ERGO desk is not compatible of the bat by simply pluging in a ethernet cable.

But seeing that it had 5V, RX and TX pins made me hopeful so I got a RJ45 breakoutboard and tried to make a cable that would match the pinout out the ROL ERGO controller with what Upsy-Desky needs. However I have had no luck so far.

What I noted was that the 5V from the ROL ERGO controller drops to bellow 1V when I connect Upsy-Desky so I assume the 5V from the controller is powerful enough to handle data signals and not to drive the Upsy-Desky. To get around this and troubleshoot I simply attached usb power to Upsy-Desky while everything was connected to the ROL ERGO controller.

Worth noting could be that from the picture of inside the keypad the desk will move up if red+green wire is shorted and it will move down if the white+green wire is shorted.

Do you think there is a chance to get this desk working with Upsy-Desky, and how could I then assist in the troubleshooting?

magnussp, 2023-03-06:
@tjhorner tell me if there is something I can assist with to see if it would even be possible to add support for this desk.

tjhorner, 2023-03-07:
So sorry I missed this! I will review what you've posted tomorrow and let you know.

dcobbley, 2023-03-23:
I have the ROL ECS+ controller and have not had luck yet cracking the exact UART communication settings yet. My RJ45 pinouts are unlabeled so it has taken me some time to trace the PCB and figure out which lines represent RX,TX, etc.

Please take a photo of your entire PCB (top & bottom), as high resolution as you can. It will help me compare against my setup (and hopefully provide helpful info back to you) which uses the [PIC18F26K22](https://www.microchip.com/en-us/product/PIC18F26K22) in the main controller, and the [PIC16F1938](https://www.microchip.com/en-us/product/PIC16F1938) in the handset.

Reading through the manual of the ROL ERGO GF-470, it looks like all the handset does is provide an up/down button to manually control height as well as providing a way to set two height limits when both up & down are pressed simultaneously.

I could be way off here, but I wonder if you could simplify making your controller 'smart' by simply not using the UART portion of upsy-desky and only rely upon the GPIO's to press the up/down button for x seconds at which point the desk controller will automatically stop the desk at the originally programmed height. You could even prototype this with any ESP dev board if you haven't yet purchased an Upsy-Desky board.

magnussp, 2023-04-20:
@dcobbley sry for the late reply. Here are some pics of the entire board in my ROL ERGO desk.

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

Your observation from the manual is correct. I have been thinking of this solution as well to just connect GPIO to the original controller and then set min and max limits in the oem way for the desk and control it this way. But would be cool to get that working through Upsy-Desky 🙂

CM000n, 2024-01-10:
There are now also some instructions for assembling your own controller for ROL ERGO tables using an RJ45 extension cable and an ESP device: https://github.com/jensihnow/smarthome/blob/main/smartdesk/README.md
These ROL ERGO controllers are also used for IKEA Rodulf tables.
Compatibility with Upsy Desky should therefore be "theoretically" possible. 😉

Xavantex, 2024-12-21:
As it seems ROL ERGO just have binary on/off for up and down, is upsy-desky even compatible with some manual labor?

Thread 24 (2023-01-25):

Desk Height not being reported

p-rintz, 2023-01-25:
Hi there,

thank you for the great product, first.

Ive been using it without a problem since it arrived, sadly, since updating all my ESPhome controllers yesterday, the upsy-desky stopped reporting the desk height. It still works otherwise, but it only shows N/A for the height.

Rolling back to the firmware uploaded to Github has not helped this.

Please do not hesitate to tell me what further information you need. Thank you!

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

tjhorner, 2023-01-26:
Is the decoder set correctly? I wonder if the update has reset it back to the default.

Is there anything interesting in the logs? Errors or such would be helpful

Try using this tool to entirely reflash and see if it works: https://shop.horner.tj/things/upsy-desky/setup/stock

p-rintz, 2023-01-26:
I already tried setting the decoder and the units to uplift/inches and back again, and have tried it again just now, sadly, that hasn't helped.

I will try reflashing it later today.

p-rintz, 2023-01-26:
Well, I couldnt wait. So I tried reflashing it just now via the browser, but it hasnt helped either, sadly.

Should I try flashing the debug firmware that you have on the release page?

dominiclesinski, 2023-01-27:
just gonna jump in here rather than opening a separate issue because I also have a problem with desk height reporting. I changed it to cm but it only changed the unit rather than the actual number so I now get 28cm rather than 28in, while in reality it should be  71cm :) any advice? ty!

p-rintz, 2023-01-27:
> just gonna jump in here rather than opening a separate issue because I also have a problem with desk height reporting. I changed it to cm but it only changed the unit rather than the actual number so I now get 28cm rather than 28in, while in reality it should be 71cm :) any advice? ty!

Restart the upsy-desky. It should work afterwards.

dominiclesinski, 2023-01-27:
thanks for trying to help, tried that already several times with the same result...
firmware version is : 2022.10.1

junoatwork, 2023-01-27:
Came here after noticing the same "NA" reading. The keypad on my desk says "jarvis", and when I bought the desk the brand name was under "jarvis", so naturally I chose the "jarvis" decoder in the upsy-desky web interface.

However, after further investigating the control unit under my desk (googling the model number model: `jcb36n2a`) turns out to be "uplift" - changing to that decoder works, and now the number reported by the sensor matches what's shown on the lcd on the original keypad.

Posting in case it helps anyone else!

p-rintz, 2023-01-27:
@junoatwork thank you. While this wasnt the issue I had (as it worked previously as well, with the jarvis decoder), your comment helped me in fixing my issue.
I hadn't looked at the control unit since installing the upsy-desky (because it just works so well), but for some reason the control unit itself seemed to have "bugged" out after the update and wasn't displaying the height itself anymore either.

After unplugging and re-plugging the control unit into the upsy-desky, it started working again.

Not entirely sure how it happened or if this can happen regularly.

While my issue obviously is "solved", Ill keep this open for now for @tjhorner to pipe in, in regards to this potentially being some bug with the upsy-desky.

p-rintz, 2023-01-27:
> just gonna jump in here rather than opening a separate issue because I also have a problem with desk height reporting. I changed it to cm but it only changed the unit rather than the actual number so I now get 28cm rather than 28in, while in reality it should be 71cm :) any advice? ty!

I also just re-read your comment. Sorry, I misunderstood you earlier. I had a similar "display" issue, but that isnt what you meant, if I read your comment correctly now. You probably need to change the decoder. Uplift --> Jarvis or the other way around.

tjhorner, 2023-01-28:
I'm glad you got it fixed @p-rintz, and thanks for posting your solution! I will go ahead and add this to the troubleshooting documentation in case others encounter something similar.

p-rintz, 2023-01-28:
If you dont think this is something that could have been triggered by the upsy-desky, feel free to close this issue @tjhorner

Thank you again for the great product. :+1:

Closed 2023-02-07.

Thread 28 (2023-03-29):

Desk height and all other entities always eventually become unknown in Home Assistant

grahamwetzler, 2023-03-29:
Running version 1.0.0 with an Uplift Desk (FRM053-2). After a day or so all of the entities in Home Assistant become unknown. The buttons still work to change the desk height though. The only way to temporarily fix this is to re-plug the Upsy Desky.

I don't see any useful logs to add.

davewongillies, 2023-04-01:
I'm seeing this too but in my case re-plugging the Upsy Desky doesn't bring the entities back. HA can't see anything from it anymore besides the Status LED and Re-Detect Encoder entities. I can still operate the Upsy Desky from its web UI. I've got this connected to a Fully Jarvis desk.

davewongillies, 2023-04-01:
> I'm seeing this too with 1.0.0 but in my case re-plugging the Upsy Desky doesn't bring the entities back. HA can't see any entities from it anymore besides Status LED and Re-Detect Encoder. I've also done a factory firmware flash and its made no difference.
>
> I can still operate the Upsy Desky from its web UI. I've got this connected to a Fully Jarvis desk.

I ended up completely remove my upsy desky from HA to get it working again.

tjhorner, 2023-04-01:
> HA can't see any entities from it anymore besides Status LED and Re-Detect Encoder

That's strange, were the old entities "unknown" or "unavailable"?

tjhorner, 2023-04-01:
@grahamwetzler In the history of the entities which become "unknown", do they become "unavailable" for a brief time beforehand?

grahamwetzler, 2023-04-01:
I'm not sure. Earlier today I moved away from the ESPHome configuration method and flashed 0.4.1 from the Github releases and it's been fine.

grahamwetzler, 2023-04-07:
It took a week of but it just happened to me on version 0.4.1. The entities all became unavailable then unknown. I guess I'll try version 1.0 again and see if it happens there.

grahamwetzler, 2023-05-05:
Unfortunately this is still happening on the version 1.0 file I downloaded from the Github release. Even using the reboot from the web ui does not bring back the entities in Home Assistant. The only way to temporarily get it to work is to replug the RJ45 connector.

tjhorner, 2023-05-25:
Sorry to leave you hanging here. If you're still experiencing this issue, I would suggest powering the device with an external USB power supply. Since the entities first become unavailable (indicates the device is totally unreachable) this suggests to me that your desk's control box may not be able to provide enough current to keep the Upsy Desky powered. Providing the additional power supply via USB-C will resolve this.

Let me know how it goes. If you still experience this after plugging a USB-C power cable, try installing the debug firmware from the [releases](https://github.com/tjhorner/upsy-desky/releases/tag/v1.1.1). Grab `debug-firmware.bin` and flash that via OTA. It will provide additional information in the logs, such as why the device was reset.

grahamwetzler, 2023-06-03:
I believe I've come up with a workaround. I added an automation where any time the desk height becomes unavailable, I trigger a button press on the re-detect decoder button.

grahamwetzler, 2023-06-20:
Unfortunately my workaround did not work. Even if provided with an extra source of power via the USB-C port, it still goes completely unresponsive where the only fix is to unplug/replug the RJ-45 connector. I'm going to try the debug firmware again and hopefully something will show up in the log.

grahamwetzler, 2023-06-20:
I do see an issue right away. When first started, `Decoder detection complete. Correct decoder variant: uplift` showed up in the log. A few hours later I saw the height go unavailable in Home Assistant. I pressed a preset on my desk and I saw `Decoder detection complete. Correct decoder variant: omnidesk` pop up in the log

tjhorner, 2023-06-20:
Can you provide the information that appears in the "Device Info" sensor? I'm interested in the reset reason. It sounds like it might be restarting in the middle of the control box sending messages, and fail to detect the correct protocol.

Also, what is the model number for your keypad?

grahamwetzler, 2023-06-20:
This info?
```
Firmware: 2023.2.4 (Mar 12 2023, 21:54:19)
Hardware: 1.0.0
```

I have [this keypad](https://www.upliftdesk.com/advanced-comfort-angled-keypad-by-uplift-desk/)

tjhorner, 2023-06-20:
There should be a sensor called "Device Info" under "Diagnostics" in Home Assistant (though, it looks like it's truncated to just "D..." because the value is so long lol):

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

grahamwetzler, 2023-06-21:
Oh I see,
```
2023.5.3|Flash: 4096kB Speed:40MHz Mode:DIO|Chip: ESP32 Features:WIFI_BGN,BLE,BT, Cores:2 Revision:3|ESP-IDF: v4.4.2|EFuse MAC: 3C:E9:0E:8B:49:D0|Reset: Software Reset CPU|Wakeup: Unknown
```

tjhorner, 2023-06-23:
Thanks for that. I'm not seeing any abnormal reset reason, which is strange. Can you try out this firmware? It bypasses detection and forces it to use the `uplift` decoder.

[firmware.bin.zip](https://github.com/tjhorner/upsy-desky/files/11850268/firmware.bin.zip)

grahamwetzler, 2023-06-23:
Thanks, I installed that firmware

grahamwetzler, 2023-06-30:
Unfortunately the current height and other entities are still going unknown after a few days. Once I press a key on the desk, the height does come right back at least.

amalafrozalam, 2024-01-09:
Coming here to report that this problem is still occurring on Version 2.0.0 of the firmware. I have a Fully Jarvis desk setup and I can control the desk for a while, and then the Upsy goes offline. No explanation why.

brettinternet, 2024-03-09:
I'm also seeing this issue with similar logs. I have the same keypad.

ESPHome appears to frequently disconnect from a wireless connect to the device, but I'm not sure that's related:

```
ERROR Error sending data: [Errno 104] Connection reset by peer
```

tjhorner, 2024-03-09:
@brettinternet can you confirm whether the state is changing to `unknown` or `unavailable`?

brettinternet, 2024-03-09:
@tjhorner The Home Assistant state is `Unknown` with periodic history (detected for a short time while it's moving up or down). And the "Desk Height" state on the web server shows `NA`.

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

tjhorner, 2024-03-09:
@brettinternet Thanks for the info. How often do you see the entities becoming `unavailable`? Could you open the ESPHome logs and press the "Re-Detect Decoder" button entity, then share what the output from the logs is?

tjhorner, 2024-03-09:
Since multiple people have run into this issue, I created this guide just now to assist in log collection etc: https://upsy-desky.tjhorner.dev/docs/troubleshooting/connection-issues/

brettinternet, 2024-03-10:
Here are some details:

###### Controller

Uplift FRM053-2. The desk is almost 2 years old.

###### Keypad

FRM066 "Advanced Comfort Angled Keypad".

###### Device Info

`2024.2.2|Flash: 4096kB Speed:40MHz Mode:DIO|Chip: ESP32 Features:WIFI_BGN,BLE,BT, Cores:2 Revision:3|ESP-IDF: v4.4.2|EFuse MAC: 08:B6:1F:76:D8:7C|Reset: Software Reset CPU|Wakeup: Unknown`

---

Yesterday I noticed the device was offline in ESPHome despite being able to connect to it via ESPHome and view the logs. It looks like this is sometimes an mDNS issue (despite running the ESPHome container in network_mode "host" and having an mDNS repeater). As a workaround, I added a manual IP in the ESPHome config:

```yaml
wifi:
  ssid: !secret wifi_ssid
  password: !secret wifi_password

  manual_ip:
    static_ip: <upsy desky static IP>
    gateway: <gateway>
    subnet: <subnet>
```

This appeared to stabilize the connection for much longer than a mere few minutes as I was experiencing before. Only just now, almost a full day later, have I seen the entities revert back to `unknown` and `unavailable`.

The first two lines of the logs below represent when the Desk Height becomes `unknown` in Home Assistant (or `NA` on Upsy Desky state). The second decoder detection is after I've hold the desk keypad elevation arrows up and down a few times:

```
13:52:36 | [I] | [standing_desk_height:036] | Starting decoder detection
-- | -- | -- | --
13:52:39 | [W] | [standing_desk_height:044] | No valid decoder found. Please make sure your desk is reporting the height and you can see it on the keypad
13:57:17 | [I] | [standing_desk_height:036] | Starting decoder detection
13:57:18 | [I] | [standing_desk_height:094] | Decoder detection complete. Correct decoder variant: uplift
13:57:18 | [I] | [standing_desk_height:095] | If you want to make this change permanent, add the following to this sensor's configuration:
13:57:18 | [I] | [standing_desk_height:096] | variant: uplift
```
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
brettinternet, 2024-03-14:
Here's a workaround in Home Assistant:

```yaml
# configuration.yaml

template:
  - trigger:
      - platform: state
        entity_id: sensor.upsy_desky_desk_height
        not_to:
          - unknown
          - unavailable
    sensor:
      - name: Desk Height
        state: '{{ trigger.to_state.state }}'
        device_class: distance
        unit_of_measurement: 'in'
```

This creates a sensor `sensor.desk_height` which uses the last value that isn't `unknown` or `unavailable`.

tjhorner, 2024-04-22:
Hi everyone, I've got some more details that hopefully brings us closer to a fix. One person experiencing this issue was able to capture a backtrace at the time of disconnection, and it appears that the BLE component is to blame, but not in the way initially thought. Here is the trace:

```
0x40083815: panic_abort at panic.c:402
0x400987bd: abort at abort.c:46
0x401fe9c7: __cxxabiv1::__terminate(void (*)()) at eh_terminate.cc:47
0x401fea0e: std::terminate() at eh_terminate.cc:57
0x401feb07: __cxa_throw at eh_throw.cc:95
0x401fea66: operator new(unsigned int) at new_op.cc:54
0x400df22d: esphome::esp32_ble::ESP32BLE::gap_event_handler(esp_gap_ble_cb_event_t, esp_ble_gap_cb_param_t*) at ble.cpp:309
0x4013378d: btc_gap_ble_cb_to_app at btc_gap_ble.c:55
 (inlined by) btc_gap_ble_cb_handler at btc_gap_ble.c:1156
0x4015c69d: btc_thread_handler at btc_task.c:196
0x4015e513: osi_thread_run at thread.c:68
```

There are some issues with similar stack traces in the ESPHome repo itself (e.g., https://github.com/esphome/issues/issues/4901) and the conclusion appears to be that the device is running out of RAM. This is not surprising to me, due to the overhead of the Arduino framework and all the components the stock firmware has.

I will dig a little deeper into this to verify that this is indeed the cause, but I'm just happy that we aren't flying blind anymore! I suspect a solution to this may involve trimming down the stock firmware and offering a sort of "build your own Upsy Desky firmware" tool where one can include extra features from ESPHome if one wishes.

In the meantime, I will try to replicate the issue with this new information and report back.

dwardu89, 2024-04-22:
@tjhorner  So if i were to disable the bluetooth proxy feature, it should hopefully not crash? I'm going to try it out right now and ill get back to you on the outcome after a while testing.
I noticed, the display also stops showing the height and doesnt turn off the LEDs when it did before. That crash might be the cause of it.

tjhorner, 2024-06-06:
Hi everyone. I just published v3.0.0 of the firmware, which includes changes that are likely to solve this issue.

Please read the release notes and try it out: https://github.com/tjhorner/upsy-desky/releases/tag/v3.0.0

Thanks!

rotx, 2025-03-06:
For me, this still happens with version 4.0.2. The ESP32 stays online with its IP but vanishes from MDNS, which means that Home Assistant marks it as unavailable. I tried a number of suggestions that didn't work. This seems to happen with the IDF framework on ESP32 and is not specific to the Upsy Desky. The one thing that finally worked was:

wifi:
  power_save_mode: none

(I had to modify version of stock.yaml since it's incompatible with BLE)

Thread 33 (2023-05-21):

Show current firmware version for OTA update

tomtastic, 2023-05-21:
Would it be possible to add details of the current firmware version to the web interface ?
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

tomtastic, 2023-05-23:
Very nice, thank you!

tomtastic, 2023-05-23:
Just updated OTA, tried restarting, etc, but nothing new showing...

tjhorner, 2023-05-23:
Oh, sorry about that — made a silly mistake and forgot something. I'll re-release as 1.1.1 shortly.

tomtastic, 2023-05-23:
`v1.1.1` Works perfectly, thank you for the fast implementation!

Closed 2023-05-23.

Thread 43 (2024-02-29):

Does it support WP-CB01 Control box?

oeloo, 2024-02-29:
Hi, I have a desk with a WP-CB01 Control box, is upsy-desky able to control it?
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

tjhorner, 2024-03-01:
This model number doesn't appear in the [compatibility list](https://upsy-desky.tjhorner.dev/docs/reference/compatibility/) so I can't guarantee that it will. However, please check out the [compatibility assessment guide](https://upsy-desky.tjhorner.dev/docs/reference/compatibility/assessing-compatibility/) — it includes useful information on how to determine if it may be compatible

oeloo, 2024-03-01:
I have looked at the guide and checked my Control box: the port that communicate with the keypad has 10 pins, so it is slightly different from an Ethernet jack. If I read correctly this means it means there is no chance it will work 😟

tjhorner, 2024-03-01:
That's correct, if it uses either of the outer-most of the 10 pins then I'm afraid it won't work 😔

oeloo, 2024-03-01:
The outer-most are fired on the port end, I don't know if they are wired inside the remote control PCB (as there is no screws or anything to open it safely without destroying it) but I guess it is otherwise they would have chosen a RJ45 plug I suppose.
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

tomas1808, 2025-05-09:
Hey @tjhorner just received my Upsy Desky! I YOLO'd it hoping that my desk would be compatible but it wasn't lol. I have the same controller as OP with the 10-pin cable.

My idea is to change the wiring to make it work. I will remove the 10-pin cable from the keypad and replace it with a standard 8-pin RJ45 with the correct remapping of pins. This should be able to connect correctly to Upsy Desky. Then I'll use the 10-pin cable to make a "8-pin to 10-pin" cable so that I can hook Upsy Desky to the controller box without having to mod the controller box itself.

I have already identified +5V and GND pins (pins 9 and 6 respectively on the 10-pin cable). My only question to you @tjhorner is: If I correctly set up the +5V and GND pins to be compatible with Uspy Desky, can the remaining data pins be detected by Upsy Desky and "remapped" by software? I really don't want to take out my logic analyzers to figure out the rest of the pins lol.

Thanks!

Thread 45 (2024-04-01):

Clarify BOM for manufacturing PCB

Crazyphil, 2024-04-01:
### Troubleshooting Guide

- [X] I have followed the steps in the troubleshooting guide and my issue is either not listed or is not solved.

### Description

I'm trying to assemble a PCB order directly from a PCB manufacturer (not because I don't like you earning some money off this project, but because shipping and importing from the USA to Europe is more pain than ordering from China). During the process I noticed some inconsistencies in the component descriptions in the KiCad project, the BOM file from Tindie and the actual packages on the PCB.

- Component `D1` is marked as _1N5817_, but this component as well as the linked datasheet on Tindie refer to a through-hole part. The PCB, however, clearly needs an SMD part, so shouldn't this component more likely be a _1N5819WS_?
- Component `U1` is marked as _CP2102N-Axx-xQFN28_, which has a QFN28 package with 7 pins per edge. However, the PCB has 8 pins per edge, so I would actually need a _CP2102N-Axx-xQFN24_ chip, no?

Also, a bit more information in regards to how to order the PCB at the manufacturer of your choice would be nice, although I do understand if you wouldn't like to do that because of the support effort this could create. However, you could still profit from referrals. A great example in my opinion is the [Valetudo Dreame Breakout PCB](https://github.com/Hypfer/valetudo-dreameadapter) for the [Valetudo](https://valetudo.cloud) project, where there is even a community of people sharing their PCBs (not a use-case for upsy-desky, of course) and consolidating orders for reduced shipping cost.

### Logs

_No response_

### Which version of the Upsy Desky firmware config are you running?

_No response_

### How do you manage your Upsy Desky's updates?

None

### If you're using an ESPHome YAML config, which version of ESPHome are you running?

_No response_

### ESPHome Config

_No response_

tjhorner, 2024-04-01:
>Component `D1` is marked as _1N5817_, but this component as well as the linked datasheet on Tindie refer to a through-hole part. The PCB, however, clearly needs an SMD part, so shouldn't this component more likely be a _1N5819WS_?

Yes, that's correct. I'll update the BOM.

>Component `U1` is marked as _CP2102N-Axx-xQFN28_, which has a QFN28 package with 7 pins per edge. However, the PCB has 8 pins per edge, so I would actually need a _CP2102N-Axx-xQFN24_ chip, no?

No, the QFN-28 package is correct. You might have mis-counted the pins — there are 7 per edge on `U1`.

I'll see what I can do regarding more information on self-ordering a PCB from a manufacturer, but my time to work on this project is very limited at the moment. If you are ordering from JLCPCB, you can use the `LCSC` row in the BOM to correlate each part with the correct part from their inventory. Those are the exact parts I use in the pre-assembled units.

Crazyphil, 2024-04-02:
Thank you for the quick response.

> No, the QFN-28 package is correct. You might have mis-counted the pins — there are 7 per edge on `U1`.

That was my fault, I had it the other way round: The footprint was correct, but the MPN referenced a part with package QFN24 (_CP2102N-A02-GQFN24_). As I've seen from the commit, you've spotted that already.

> I'll see what I can do regarding more information on self-ordering a PCB from a manufacturer, but my time to work on this project is very limited at the moment.

I understand, time is a very precious resource indeed :smile: An alternative I came upon during my research could be PCBWay's [Shared Projects](https://www.pcbway.com/project/) that offer preconfigured public PCB (and assembly) orders and a small 10% commission to the project's author for every order. That way, users wouldn't have to deal with configuring the project for themselves. However, the minimum order amount of 5 PCBs still applies.
After comparing multiple services I can say that their offers are competitively priced, and they even offer shipping under the IOSS scheme for EU customers, which takes care of any taxes and import hassles.

> If you are ordering from JLCPCB, you can use the `LCSC` row in the BOM to correlate each part with the correct part from their inventory. Those are the exact parts I use in the pre-assembled units.

In that regard, there's one more thing I've found which I forgot to mention: in in the BOM, the LCSC number is equal for both `R18` (1kΩ) and `R22` (940Ω). I remember darkly from my electronics course a few years ago that resistor values aren't necessarily that exact and therefore interchangeable in a certain range. However, if in this case it really doesn't matter whether to use two different components or just one, why not simplify it formally on the PCB instead of only in the BOM?

sibero80, 2024-04-29:
+1 on the PCBWAY Shared Projects idea. I'm located in South America, and getting things shipped from China vs Europe/USA is orders of magnitude easier and cheaper. I'd gladly pay 10% or 20% over PCB and parts costs if it goes to the designer.

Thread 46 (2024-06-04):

Wireless ESPHhome Update fails, connection reset by peer

plaetzchen, 2024-06-04:
### Troubleshooting Guide

- [X] I have followed the steps in the troubleshooting guide and my issue is either not listed or is not solved.

### Description

When trying to update with the newest ESPHome version I get an error after upload that says "Connection reset by peer". The update might be installed (since the newest version is showing up in the device log) but HA still wants to install an update. Cleaning the build cache of ESPHome does not help.

### Logs

```plain text
Upsy-Desky:

INFO ESPHome 2024.5.4
INFO Reading configuration /config/esphome/upsy-desky-76db98.yaml...
INFO Starting log output from 10.0.0.94 using esphome API
INFO Successfully connected to upsy-desky-76db98 @ 10.0.0.94 in 0.068s
INFO Successful handshake with upsy-desky-76db98 @ 10.0.0.94 in 0.121s
[09:45:17][I][app:100]: ESPHome version 2024.5.2 compiled on May 21 2024, 11:25:44
[09:45:17][I][app:102]: Project tj_horner.upsy_desky version 2.0.0
[09:45:42][I][standing_desk_height:036]: Starting decoder detection
[09:45:42][I][standing_desk_height:094]: Decoder detection complete. Correct decoder variant: jarvis
[09:45:42][I][standing_desk_height:095]: If you want to make this change permanent, add the following to this sensor's configuration:
[09:46:18][W][component:157]: Component ota set Warning flag: unspecified
[09:46:18][E][component:164]: Component ota set Error flag: unspecified
[09:46:18][W][component:237]: Component ota took a long time for an operation (201 ms).
[09:46:18][W][component:238]: Components should block for at most 30 ms.
[09:46:23][E][component:176]: Component ota cleared Error flag

Build:

INFO ESPHome 2024.5.4
INFO Reading configuration /config/esphome/upsy-desky-76db98.yaml...
INFO Generating C++ source...
INFO Compiling app...
Processing upsy-desky-76db98 (board: esp32dev; framework: arduino; platform: platformio/espressif32@5.4.0)
--------------------------------------------------------------------------------
HARDWARE: ESP32 240MHz, 320KB RAM, 4MB Flash
 - toolchain-xtensa-esp32 @ 8.4.0+2021r2-patch5
Dependency Graph
|-- AsyncTCP-esphome @ 2.1.3
|-- WiFi @ 2.0.0
|-- FS @ 2.0.0
|-- Update @ 2.0.0
|-- ESPAsyncWebServer-esphome @ 3.2.2
|-- DNSServer @ 2.0.0
|-- ESPmDNS @ 2.0.0
|-- noise-c @ 0.1.4
|-- ArduinoJson @ 6.18.5
|-- Improv @ 1.2.3
RAM:   [==        ]  16.3% (used 53456 bytes from 327680 bytes)
Flash: [========= ]  94.5% (used 1733837 bytes from 1835008 bytes)
========================= [SUCCESS] Took 5.69 seconds =========================
INFO Successfully compiled program.
INFO Connecting to 10.0.0.94
INFO Uploading /data/build/upsy-desky-76db98/.pioenvs/upsy-desky-76db98/firmware.bin (1739616 bytes)
ERROR Error binary size: Unknown error from ESP
```

### Which version of the Upsy Desky firmware config are you running?

_No response_

### How do you manage your Upsy Desky's updates?

None

### If you're using an ESPHome YAML config, which version of ESPHome are you running?

_No response_

### ESPHome Config

```YAML
substitutions:
  name: upsy-desky-76db98
  friendly_name: Upsy Desky 76db98
packages:
  tj_horner.upsy_desky: github://tjhorner/upsy-desky/firmware/stock.yaml@v2.0.0
esphome:
  name: ${name}
  name_add_mac_suffix: false
  friendly_name: ${friendly_name}
api:
  encryption:
    key: YesItHasThat

wifi:
  ssid: !secret wifi_ssid
  password: !secret wifi_password
```

tjhorner, 2024-06-06:
If you are running into this error, I would recommend flashing via the USB-C port on the device. The module used on the board is pretty resource-constrained and the stock firmware has many components that may be unnecessary after first-use. For this reason, it likely runs out of RAM during an OTA flash (without inspecting the logs via USB during an OTA, it's hard to tell).

I recommend "trimming" the firmware by following this guide: https://upsy-desky.tjhorner.dev/docs/advanced/customization/#trimming-the-firmware

Then flash the resulting firmware via USB. From then on, OTAs should work.

wez, 2024-12-26:
turning off wifi power saving can also help with spotty ota: https://github.com/tjhorner/upsy-desky/issues/55#issuecomment-2423364079

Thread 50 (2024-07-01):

Link to case files on BYOE page of the Upsy Desky site contains an extra trailing slash

nevvob, 2024-07-01:
I printed my own enclosure but notice that the link to the file on the page https://upsy-desky.tjhorner.dev/docs/byoe/ has an extra trailing slash meaning that the file does not download:

[Download STL Files](https://upsy-desky.tjhorner.dev/assets/files/enclosure-b738eb46a745e9499b85d6a1623c30b5.zip/) should be [Download STL Files](https://upsy-desky.tjhorner.dev/assets/files/enclosure-b738eb46a745e9499b85d6a1623c30b5.zip)

tjhorner, 2024-07-01:
Thanks for flagging this! It's an ongoing issue with the docs platform I use combined with the fact that it's hosted on GitHub Pages.

I'll try to find a workaround in the meantime.

nevvob, 2024-07-01:
My bad - sorry!

Thanks for creating an awesome device that worked straight out of the box.  I am genuinely impressed with the tolerances you've achieved on the printed case.

tjhorner, 2024-07-01:
Thank you for the kind words! I'm glad everything worked straight away for you :)

I just deployed a fix for this issue, seems like file download links work properly now. Thanks again for reporting it.

Closed 2024-07-01.

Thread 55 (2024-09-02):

Recurring connection errors

jhemak, 2024-09-02:
### Troubleshooting Guide

- [X] I have followed the steps in the troubleshooting guide and my issue is either not listed or is not solved.

### Description

Hello, over the past couple weeks I have started to see errors like this in my log.  Any idea what may cause or fix it?

```
2024-09-02 10:16:42.686 WARNING (MainThread) [aioesphomeapi.connection] upsy-desky @ IP: Connection error occurred: Ping response not received after 90.0 seconds
2024-09-02 10:17:46.818 WARNING (MainThread) [homeassistant.components.esphome.manager] Error getting setting up connection for IP: Timeout waiting for ListEntitiesDoneResponse, ListEntitiesAlarmControlPanelResponse, ListEntitiesBinarySensorResponse, ListEntitiesButtonResponse, ListEntitiesCameraResponse, ListEntitiesClimateResponse, ListEntitiesCoverResponse, ListEntitiesDateResponse, ListEntitiesDateTimeResponse, ListEntitiesEventResponse, ListEntitiesFanResponse, ListEntitiesLightResponse, ListEntitiesLockResponse, ListEntitiesMediaPlayerResponse, ListEntitiesNumberResponse, ListEntitiesSelectResponse, ListEntitiesSensorResponse, ListEntitiesServicesResponse, ListEntitiesSirenResponse, ListEntitiesSwitchResponse, ListEntitiesTextResponse, ListEntitiesTextSensorResponse, ListEntitiesTimeResponse, ListEntitiesUpdateResponse, ListEntitiesValveResponse after 60s
2024-09-02 10:17:56.820 ERROR (MainThread) [aioesphomeapi.connection] upsy-desky@IP: disconnect request failed: Timeout waiting for DisconnectResponse after 10.0s
```

### Logs

_No response_

### Which version of the Upsy Desky firmware config are you running?

4.0.0

### How do you manage your Upsy Desky's updates?

OTA Updates

### If you're using an ESPHome YAML config, which version of ESPHome are you running?

_No response_

### ESPHome Config

_No response_

tjhorner, 2024-09-02:
Are these errors being manifested through any symptoms like unavailable or unknown sensors?

jhemak, 2024-09-02:
Yes, I believe so. The sensors go unavailable around the same time and then unknown a few minutes later.

jhemak, 2024-09-02:
OK ... just confirmed... when this error occurs in the logs, all sensors in the UI go unavailable.  A few minutes later, some sensors go to unknown (e.g. preset_1) and others go to their actual values (e.g. max_target_height).

tjhorner, 2024-09-02:
Thanks for confirming. I'm interested to know the following:

- How often does this occur?
- What desk model do you have?
- Are you powering the Upsy Desky directly from the desk or with a USB-C power supply?

jhemak, 2024-09-03:
It seems to happen a handful of times per day.  I'll try to keep better track over the next few days and let you know.

I have an Uplift v2.  I've had all this going for several months now but don't think I was getting this error until the past 30 days or so.

Currently powering the board directly from the desk but have tried a separate USB-C power supply over the past few days.  At first I thought that had fixed it, but after some time the errors resumed so I'm not sure it had any effect (hard to say, since it's inconsistent.)  I currently have USB-C disconnected (and also haven't seen the error since my message ~5 hours ago ... but I'm sure it will be back!)

jhemak, 2024-09-03:
OK - the answer is that this is happening quite often.  Here are some times from error to sensor recovery from just 10 hours today:

6:36:43 -> 6:36:57
9:25:06 -> 9:26:04
11:33:52 -> 11:33:59
1:11:25 -> 1:11:55
1:18:05 -> 1:19:23
1:35:47 -> 1:36:57
1:43:39 -> 1:44:22
1:57:19 -> 1:57:34
2:07:33 -> 2:09:34
2:28:21 -> 2:29:49
3:02:24 -> 3:03:31
3:11:12 -> 3:12:58
3:30:50 -> 3:31:07
3:43:33 -> 3:44:00
3:58:55 -> 3:59:33

And here are the actual log messages:
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
jhemak, 2024-10-01:
FYI ... this stopped for the past 3 weeks then restarted again yesterday.  Super strange, and I'm not really sure if there's anything you can do about it since we don't know what causes it.

Here's the most recent message:

`WARNING (MainThread) [aioesphomeapi.connection] upsy-desky-xxxxxx @ x.x.x.x: Connection error occurred: Ping response not received after 90.0 seconds`

jhemak, 2024-10-05:
Hey @tjhorner - these errors are continuing.  Has anyone else reported something like this?  Do you have any idea (or even a guess) as to whether the issue is with my device or with my Home Assistant?

Here are the unique errors I've seen in just the past couple hours, and this is with USB-C power connected:

```
WARNING (MainThread) [aioesphomeapi.connection] upsy-desky-xxxxxx @ 192.168.x.x: Connection error occurred: upsy-desky-xxxxxx @ 192.168.x.x: The connection dropped immediately after encrypted hello; Try enabling encryption on the device or turning off encryption on the client (Home Assistant 2024.10.1).
WARNING (MainThread) [aioesphomeapi.reconnect_logic] Can't connect to ESPHome API for upsy-desky-xxxxxx @ 192.168.x.x: upsy-desky-xxxxxx @ 192.168.x.x: The connection dropped immediately after encrypted hello; Try enabling encryption on the device or turning off encryption on the client (Home Assistant 2024.10.1). (HandshakeAPIError)
WARNING (MainThread) [aioesphomeapi.connection] upsy-desky-xxxxxx @ 192.168.x.x: Connection error occurred: Ping response not received after 90.0 seconds
WARNING (MainThread) [homeassistant.components.esphome.manager] Error getting setting up connection for 192.168.x.x: Timeout waiting for ListEntitiesDoneResponse, ListEntitiesAlarmControlPanelResponse, ListEntitiesBinarySensorResponse, ListEntitiesButtonResponse, ListEntitiesCameraResponse, ListEntitiesClimateResponse, ListEntitiesCoverResponse, ListEntitiesDateResponse, ListEntitiesDateTimeResponse, ListEntitiesEventResponse, ListEntitiesFanResponse, ListEntitiesLightResponse, ListEntitiesLockResponse, ListEntitiesMediaPlayerResponse, ListEntitiesNumberResponse, ListEntitiesSelectResponse, ListEntitiesSensorResponse, ListEntitiesServicesResponse, ListEntitiesSirenResponse, ListEntitiesSwitchResponse, ListEntitiesTextResponse, ListEntitiesTextSensorResponse, ListEntitiesTimeResponse, ListEntitiesUpdateResponse, ListEntitiesValveResponse after 60s
ERROR (MainThread) [aioesphomeapi.connection] upsy-desky-xxxxxx @ 192.168.x.x: disconnect request failed: [Errno 104] Connection reset by peer
WARNING (MainThread) [aioesphomeapi.reconnect_logic] Can't connect to ESPHome API for upsy-desky-xxxxxx @ 192.168.x.x: Error connecting to [AddrInfo(family=<AddressFamily.AF_INET: 2>, type=<SocketKind.SOCK_STREAM: 1>, proto=6, sockaddr=IPv4Sockaddr(address='192.168.x.x', port=6053))]: [Errno 113] Connect call failed ('192.168.x.x', 6053) (SocketAPIError)
WARNING (MainThread) [homeassistant.components.esphome.manager] Error getting setting up connection for 192.168.x.x: Timeout waiting for DeviceInfoResponse after 10.0s
ERROR (MainThread) [aioesphomeapi.connection] upsy-desky-xxxxxx @ 192.168.x.x: disconnect request failed: Timeout waiting for DisconnectResponse after 10.0s
WARNING (MainThread) [aioesphomeapi.reconnect_logic] Can't connect to ESPHome API for upsy-desky-xxxxxx @ 192.168.x.x: Error connecting to [AddrInfo(family=<AddressFamily.AF_INET: 2>, type=<SocketKind.SOCK_STREAM: 1>, proto=6, sockaddr=IPv4Sockaddr(address='192.168.x.x', port=6053))]: [Errno 113] Connect call failed ('192.168.x.x', 6053) (SocketAPIError)1
```

jhemak, 2024-10-18:
After much experimentation, I'm happy to report I seem to have found a fix!

Adding `power_save_mode: NONE` to the `wifi` section of my config appears to have resolved the problem.

tjhorner, 2024-10-19:
@jhemak Glad to hear that solved it! I'll see if this would be a reasonable addition to the stock firmware. Definitely will add it to the troubleshooting section as well.

wez, 2024-12-26:
FWIW, I also had problems with the reliability of wifi. Turning power saving off resolves them, but that is not possible to set with the stock.yaml  firmware because of: https://github.com/esphome/issues/issues/2141#issuecomment-865688582 which prevents it from being used when ble is enabled.

So I switched my config to reference the base config instead.

barndawgie, 2025-05-06:
I've had some intermittent connectivity issues as well. Based on this thread, I added the following to my YAML which _seems_ to have resolved them:
```yaml
esp32_improv: !remove

wifi:
  power_save_mode: none
```

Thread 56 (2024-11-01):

FRM053-3 Reporting incorrect Height

jrsecor, 2024-11-01:
### Troubleshooting Guide

- [X] I have followed the steps in the troubleshooting guide and my issue is either not listed or is not solved.

### Description

I flashed this to two separate devices. One is on a Varidesk for work and is working great. Today I tried to set another up with my Uplift for home. I have the FRM053-3 so it is listed as compatible. On first boot, it correctly identified the height as 47 inches (which is where I had it set on boot) but it started randomly going through heights in HA - I watched it jump around. It finally settled on 12.8 inches for some reason which is incorrect.
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

I've hit re-detect decoder a few times to try and help it (since it stopped reporting height temporarily). IT definitely thinks it is at 12.5 as when I tried to set it to 20, it went up (I had to put weight on the desk to kick in protection and prevent some mounts from hitting the ceiling)

I'm not sure what exactly to do at this point. I can't adjust any of the yaml as ESPHome does not work in the way that the documentation states within HA.

### Logs

_No response_

### Which version of the Upsy Desky firmware config are you running?

4

### How do you manage your Upsy Desky's updates?

OTA Updates

### If you're using an ESPHome YAML config, which version of ESPHome are you running?

_No response_

### ESPHome Config

_No response_

jrsecor, 2024-11-01:
It seems to settle on omnidesk on most detections, every now and then thinking it is a uplift...Problem is, I don't know how to make any detection permanent as I am fairly certain that a power loss is going to break things.

Some logs -

`<html><body>
<!--StartFragment-->
12:12:04 | [W] | [web_server_idf:070] [1;31m[httpd] [0;33m | Only application/x-www-form-urlencoded supported for POST request
-- | -- | -- | --
12:12:04 | [I] | [standing_desk_height:036] | Starting decoder detection
12:12:05 | [I] | [standing_desk_height:094] | Decoder detection complete. Correct decoder variant: omnidesk
12:12:05 | [I] | [standing_desk_height:095] | If you want to make this change permanent, add the following to this sensor's configuration:
12:12:05 | [I] | [standing_desk_height:096] | variant: omnidesk
12:12:14 | [W] | [web_server_idf:070] [1;31m[httpd] [0;33m | Only application/x-www-form-urlencoded supported for POST request
12:12:14 | [I] | [standing_desk_height:036] | Starting decoder detection
12:12:16 | [W] | [standing_desk_height:044] | No valid decoder found. Please make sure your desk is reporting the height and you can see it on the keypad
12:12:18 | [W] | [web_server_idf:070] [1;31m[httpd] [0;33m | Only application/x-www-form-urlencoded supported for POST request
12:12:18 | [I] | [standing_desk_height:036] | Starting decoder detection
12:12:19 | [I] | [safe_mode:041] | Boot seems successful; resetting boot loop counter
12:12:21 | [W] | [standing_desk_height:044] | No valid decoder found. Please make sure your desk is reporting the height and you can see it on the keypad
12:12:24 | [W] | [web_server_idf:070] [1;31m[httpd] [0;33m | Only application/x-www-form-urlencoded supported for POST request
12:12:24 | [I] | [standing_desk_height:036] | Starting decoder detection
12:12:24 | [I] | [standing_desk_height:094] | Decoder detection complete. Correct decoder variant: uplift
12:12:24 | [I] | [standing_desk_height:095] | If you want to make this change permanent, add the following to this sensor's configuration:
12:12:24 | [I] | [standing_desk_height:096] | variant: uplift

<!--EndFragment-->
</body>
</html>`

jrsecor, 2024-11-01:
[logs_jacob-desk_run.txt](https://github.com/user-attachments/files/17604081/logs_jacob-desk_run.txt)

tjhorner, 2024-11-01:
It looks like you will indeed need to make the uplift decoder permanent in the YAML.

> I can't adjust any of the yaml as ESPHome does not work in the way that the documentation states within HA.

What do you mean by this? I would definitely like to fix the documentation if anything has changed. Make sure you are going to the ESPHome Dashboard addon, not the ESPHome HA integration, to adopt and edit the config.

jrsecor, 2024-11-01:
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

I didn't have the add-on, just the integration - i fixed that and that is where that log file came from in my last reply. I set it to uplift but still am getting the jumping/incorrect data reporting

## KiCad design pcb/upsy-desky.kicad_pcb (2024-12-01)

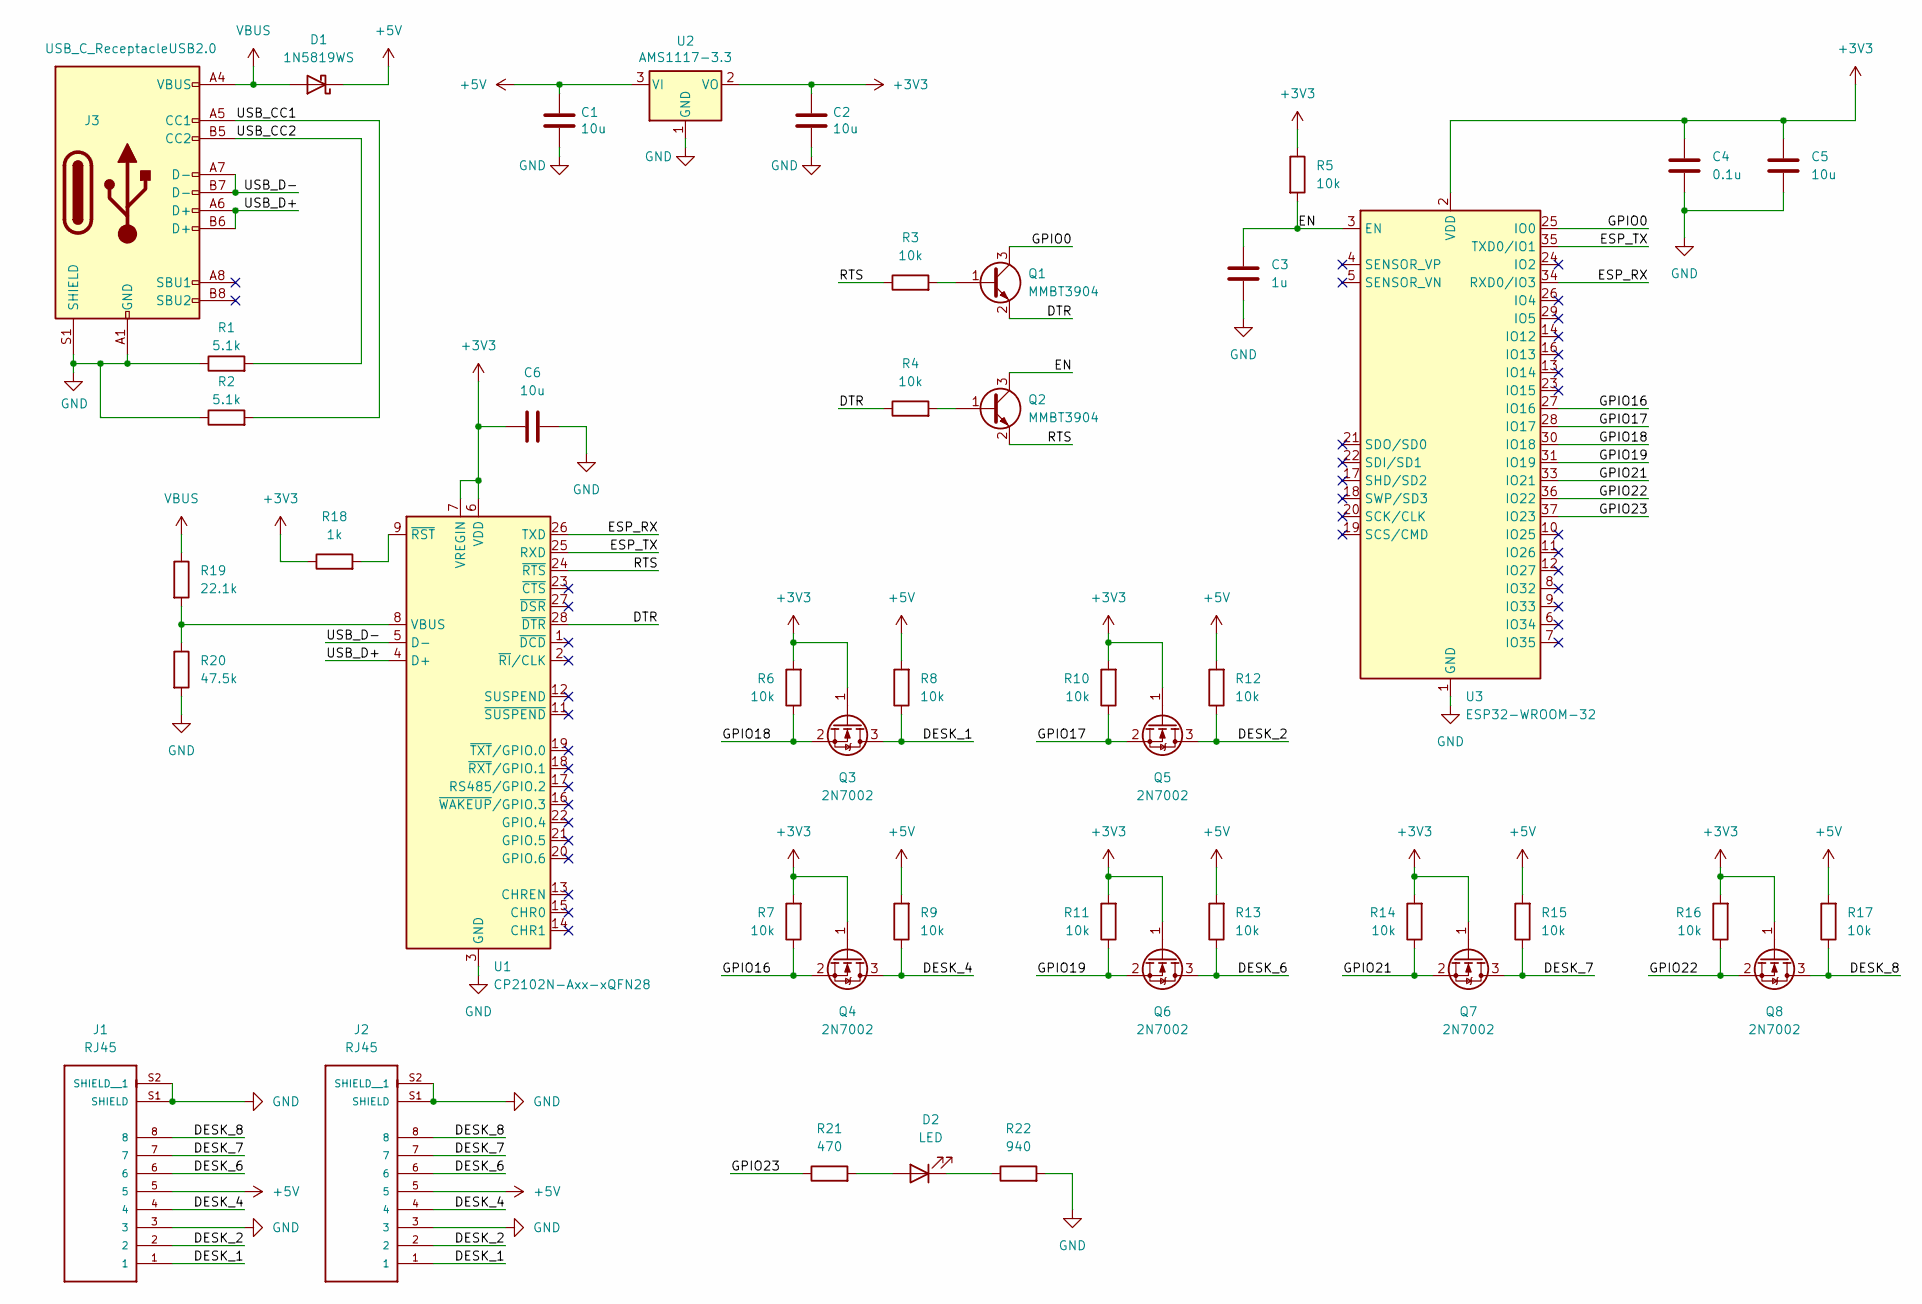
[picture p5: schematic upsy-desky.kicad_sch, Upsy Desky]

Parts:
C1, C2, C5, C6: 10u; C_0402_1005Metric; MPN GRM155R60J106ME05J; LCSC C15525
C3: 1u; C_0402_1005Metric; MPN 0402W105K100HI; LCSC C52923
C4: 0.1u; C_0402_1005Metric; MPN 0402B104K160HI; LCSC C1525
D1: 1N5819WS; D_SOD-323; MPN 1N5819WS; LCSC C191023
D2: LED; LED_0603_1608Metric; MPN LTST-C190KRKT; LCSC C2286
J1, J2: RJ45; ASSMANN_A-2004-2-4-LPS-N-R; PARTREV 00; LCSC C3000202
J3: USB_C_ReceptacleUSB2.0; USB_C_Receptacle_Palconn_UTC16-G; MPN TYPE-C-31-M-12; LCSC C165948
Q1, Q2: MMBT3904; SOT-23; MPN MMBT3904; LCSC C20526
Q3, Q4, Q5, Q6, Q7, Q8: 2N7002; SOT-23; MPN 2N7002; LCSC C8545
R1, R2: 5.1k; R_0402_1005Metric; MPN RC0402JR-075R1L; LCSC C25905
R3, R4, R5, R6, R7, R8, R9, R10, R11, R12, R13, R14, R15, R16, R17: 10k; R_0402_1005Metric; MPN RC0402JR-1310KL; LCSC C25744
R18: 1k; R_0402_1005Metric; MPN RC0402JR-131KL; LCSC C11702
R19: 22.1k; R_0402_1005Metric; MPN RC0402FR-1322K1L; LCSC C25768
R20: 47.5k; R_0402_1005Metric; MPN CR0402-FX-4752GLF; LCSC C25792
R21: 470; R_0402_1005Metric; MPN RC1005J471CS; LCSC C25117
R22: 940; R_0402_1005Metric; MPN RMCF0402FT953R; LCSC C11702
U1: CP2102N-Axx-xQFN28; QFN-28-1EP_5x5mm_P0.5mm_EP3.35x3.35mm; MPN CP2102N-Axx-xQFN28; LCSC C6568
U2: AMS1117-3.3; SOT-223-3_TabPin2; MPN AMS1117-3.3; LCSC C6186
U3: ESP32-WROOM-32; MPN ESP32-WROOM-32; LCSC C701341

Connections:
+3V3: C2.1, C4.1, C5.1, C6.1, Q3.1 (G), Q4.1 (G), Q5.1 (G), Q6.1 (G), Q7.1 (G), Q8.1 (G), R5.1, R6.2, R7.2, R10.2, R11.2, R14.2, R16.2, R18.1, U1.6 (VDD), U1.7 (VREGIN), U2.2 (VO), U3.2 (VDD)
+5V: C1.1, D1.1 (K), J1.5, J2.5, R8.2, R9.2, R12.2, R13.2, R15.2, R17.2, U2.3 (VI)
/DESK_1: J1.1, J2.1, Q3.3 (D), R8.1
/DESK_2: J1.2, J2.2, Q5.3 (D), R12.1
/DESK_4: J1.4, J2.4, Q4.3 (D), R9.1
/DESK_6: J1.6, J2.6, Q6.3 (D), R13.1
/DESK_7: J1.7, J2.7, Q7.3 (D), R15.1
/DESK_8: J1.8, J2.8, Q8.3 (D), R17.1
/DTR: Q1.2 (E), R4.1, U1.28 (~DTR)
/EN: C3.1, Q2.3 (C), R5.2, U3.3 (EN)
/ESP_RX: U1.26 (TXD), U3.34 (RXD0/IO3)
/ESP_TX: U1.25 (RXD), U3.35 (TXD0/IO1)
/GPIO0: Q1.3 (C), U3.25 (IO0)
/GPIO16: Q4.2 (S), R7.1, U3.27 (IO16)
/GPIO17: Q5.2 (S), R10.1, U3.28 (IO17)
/GPIO18: Q3.2 (S), R6.1, U3.30 (IO18)
/GPIO19: Q6.2 (S), R11.1, U3.31 (IO19)
/GPIO21: Q7.2 (S), R14.1, U3.33 (IO21)
/GPIO22: Q8.2 (S), R16.1, U3.36 (IO22)
/GPIO23: R21.1, U3.37 (IO23)
/RTS: Q2.2 (E), R3.1, U1.24 (~RTS)
/USB_CC1: J3.A5 (CC1), R2.2
/USB_CC2: J3.B5 (CC2), R1.2
/USB_D+: J3.A6 (D+), J3.B6 (D+), U1.4 (D+)
/USB_D-: J3.A7 (D-), J3.B7 (D-), U1.5 (D-)
GND: C1.2, C2.2, C3.2, C4.2, C5.2, C6.2, J1.3, J1.S1 (SHIELD), J1.S2 (SHIELD__1), J2.3, J2.S1 (SHIELD), J2.S2 (SHIELD__1), J3.A1 (GND), J3.A12 (GND), J3.B1 (GND), J3.B12 (GND), J3.S1 (SHIELD), R1.1, R2.1, R20.2, R22.2, U1.3 (GND), U1.29 (GND), U2.1 (GND), U3.1 (GND), U3.15 (GND), U3.38 (GND), U3.39 (GND)
unnamed: D2.1 (K), R22.1
unnamed: D2.2 (A), R21.2
unnamed: Q1.1 (B), R3.2
unnamed: Q2.1 (B), R4.2
unnamed: R18.2, U1.9 (~RST)
unnamed: R19.2, R20.1, U1.8 (VBUS)
VBUS: D1.2 (A), J3.A4 (VBUS), J3.A9 (VBUS), J3.B4 (VBUS), J3.B9 (VBUS), R19.1

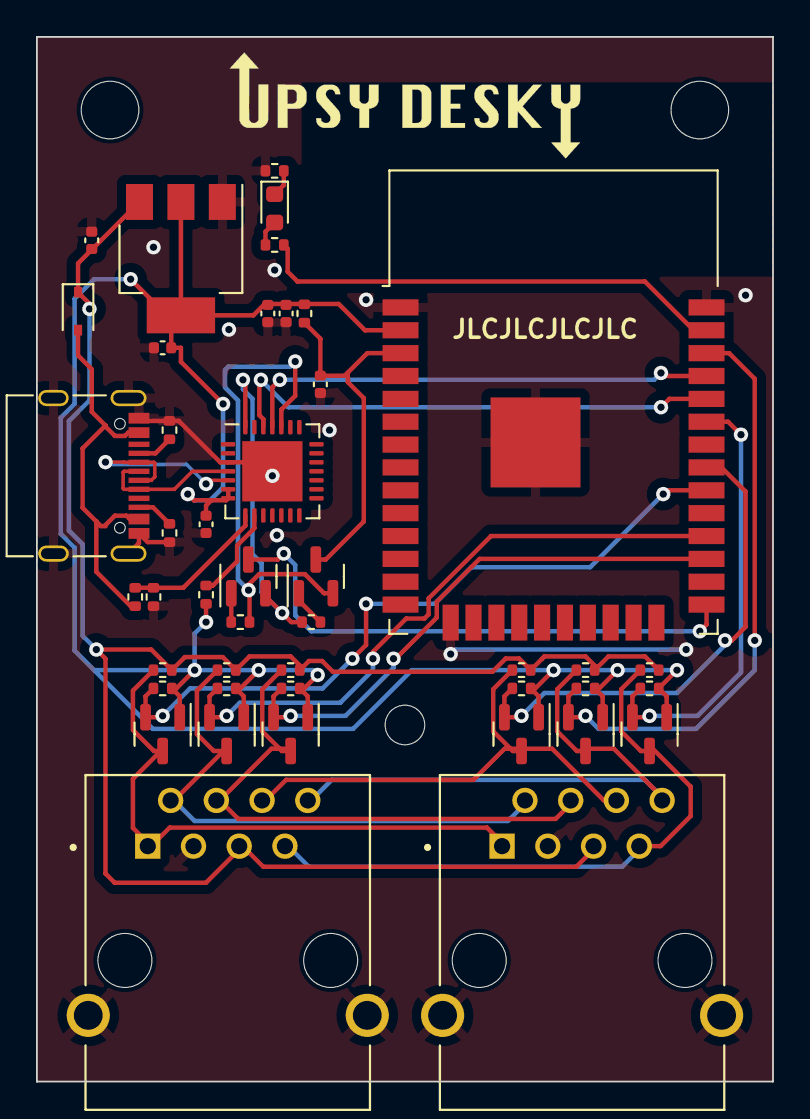
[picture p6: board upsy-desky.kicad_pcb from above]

Board: 2 copper layers, 40.9 x 58.0 mm, 45 parts (0 on the bottom side), 33 nets.

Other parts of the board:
Ref**: Val**; dark_logotype_horizontal

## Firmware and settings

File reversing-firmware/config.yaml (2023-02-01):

substitutions:
  name: "upsy-desky"

esphome:
  name: "${name}"
  name_add_mac_suffix: true

esp32:
  board: esp32dev

logger:
  level: DEBUG

# UART logging is from the perspective of the handset, i.e.:
# - TX is the data sent from the handset to the control box
# - RX is the data sent from the control box to the handset
uart:
  - # Direction: Handset -> Control Box
    id: handset_tx
    baud_rate: 9600
    rx_pin: 17
    debug: &uart_debug
      direction: RX
      dummy_receiver: true
      after:
        timeout: 50ms
      sequence:
        - lambda: UARTDebug::log_hex(uart::UART_DIRECTION_TX, bytes, ':');
  - # Direction: Control Box -> Handset
    id: handset_rx
    baud_rate: 9600
    rx_pin: 16
    debug:
      <<: *uart_debug
      sequence:
        - lambda: UARTDebug::log_hex(uart::UART_DIRECTION_RX, bytes, ':');

wifi:
  ap:
    password: "hunter2hunter2"

captive_portal:

improv_serial:

web_server:
  port: 80

ota:
  password: ""

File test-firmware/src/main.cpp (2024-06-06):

#include <Arduino.h>

#define LED_BUILTIN 23

// These correspond to RJ45 pins 1-6
int pins_to_test[] = {
  18,
  17,
  16,
  19,
  21,
  22
};

void setup() {
  Serial.begin(9600);

  pinMode(LED_BUILTIN, OUTPUT);
  
#ifdef TEST_HOST
  Serial.println("Initializing test host...");

  for (int &pin : pins_to_test) {
    pinMode(pin, INPUT);
  }

  digitalWrite(LED_BUILTIN, HIGH);

  delay(200);

  for (int &pin : pins_to_test) {
    Serial.print("Waiting for pin ");
    Serial.print(pin);
    Serial.println();

    while (digitalRead(pin) == LOW) {
      delay(50);
    }

    digitalWrite(LED_BUILTIN, LOW);
    delay(100);
    digitalWrite(LED_BUILTIN, HIGH);
  }

  digitalWrite(LED_BUILTIN, LOW);
#else
  digitalWrite(LED_BUILTIN, HIGH);

  Serial.println("Initializing test target...");

  for (int &pin : pins_to_test) {
    pinMode(pin, OUTPUT);
    digitalWrite(pin, LOW);
  }
#endif
}

void loop() {
#ifdef TEST_TARGET
  for (int &pin : pins_to_test) {
    Serial.print("Pulsing pin ");
    Serial.print(pin);
    Serial.println();

    digitalWrite(pin, HIGH);
    delay(300);
    digitalWrite(pin, LOW);
  }
#endif
}

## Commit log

2022-08-26 pcb, enclosure files
    [A-2004-2-4-LPS-N-R.step, TYPE-C-31-M-12--3DModel-STEP-56544.STEP, case.stl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]
2022-08-26 update enclosure to not model screw holes
    [case.stl]
2022-08-26 update fusion source
    [enclosure.f3z]
2022-10-01 Add test firmware and pcb changes
    [upsy-desky.kicad_sch]
2023-02-01 misc PCB updates
    [upsy-desky.kicad_pcb, upsy-desky.kicad_sch]
2023-02-01 Update enclosure STLs
    [case.stl, cover.stl]
2023-03-12 Add runtime config button to re-detect decoder
2023-05-21 Various PCB and tools changes, unrelated to firmware
    [upsy-desky.kicad_pcb, upsy-desky.kicad_sch]
2023-05-23 Switch to using second repository for project_version component
2024-04-01 Fix error in BOM - closes #45
    [upsy-desky.kicad_sch]
2024-06-06 switch to esp-idf; remove Bluetooth Proxy by default
2024-12-01 pcb: Update RJ45 part number
    [upsy-desky.kicad_pcb, upsy-desky.kicad_sch]
2024-12-01 pcb: slight revision with logo on silkscreen
    [upsy-desky.kicad_pcb]
